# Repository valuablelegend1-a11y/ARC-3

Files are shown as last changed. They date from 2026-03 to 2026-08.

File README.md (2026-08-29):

# ARC-3



## What it is:
My ARC-3 is a 3 DoF and 3 fingered robotic arm, designed to be sleek and dynamic, while also providing complete adaptability. For example, it will feature interchangeable bases, and not require wired connection to your computer. Which will allow it to be switched between multiple locations seamlessly. This simple location management, paired with a 2:1 gear ratio for finger precision, enables it to complete a multitude of tasks. Ranging from moving a heavy mug or cup across a desk, to being mounted on the wall to flip a lightswitch at the press of a button. These are only some of the potential uses, with enough setup it could do something as precise as unloading filament from a 3D printer, or even assisting with soldering. The possibilites are endless, so here's how it's set up. It will be powered by an external power socket, using a PCA9685 module to handle current, and an Arduino R4 WiFi for the controller. For the movement it will have 4 MG995 servos, one to rotate the base (yaw) two as shoulder and elbow joints (pitch) and one more, to open and close the fingers using an advanced gear system. All the wiring from these servos will run stratiegically through the center of the arm, for an impressive outside look and no movement constrictions.

## How to use it:
1. Print & assemble: all 3D parts (see `CAD/` folder) and mount the 4 MG995 servos into the printed joints.
2. Wire it up:  connect the servos to a PCA9685 servo driver, wire the PCA9685 to the Arduino R4 WiFi via I2C (SDA/SCL), and supply servo power from an external 6V power supply through the PCA9685 V+ terminal. A detailed wiring guide is in [SETUP.md](SETUP.md).
3. Flash the firmware: open `ARC3_firmware/ARC3_firmware.ino` in the Arduino IDE or upload via `arduino-cli`. The firmware includes a static IP (192.168.4.73) so the board is always reachable over WiFi. See [SETUP.md](SETUP.md) for exact steps.
4. Run the GUI: make sure Python 3 is installed (no extra packages needed), then run `python arc-3.py`. Click **CONNECT** — the app auto-discovers the board over USB or WiFi. The IP is saved automatically so you never retype it.
5. Control the arm: use the sliders, touchpad, or keyboard (Space = claw close, Ctrl = claw open). Press **EMERGENCY STOP** to freeze instantly.

For full electronics wiring, firmware configuration, power supply recommendations, and WiFi troubleshooting, see **[SETUP.md](SETUP.md)**.

## Why I am building this:
I am creating this project for a couple reasons, I don't have much CAD experience, so I am using this to learn more about the process, and how I can be more efficient with it. Ultimately to acheive my goals faster and more effectively. I also have little practice with wiring systems, I have done some light Arduino projects in the past, but nothing of this level. So I am doing my best to learn how it all works, and how I can put different things together to make something new. Another reason is to learn to code better, I have done some programming in Python, and barely scratched the surface in Arduino code, aka C/C++, so I am trying to put what I know together, and learn more along the way to expand my understanding of the languages. 

## Notes:
1. Total cost is just over $154.75 USD, however this is including 3D printer filament, which is not included in the BOM. The price discluding filament is about $88.75 USD
2. The code is using advanced IK and trigonometry functions, which are things I have not have had much time to study, therefore they may be incorrect. If so please let me know, so I can correct any issues.
3. Any further suggestions as to design or improvements are highly encouraged and greatly appreciated.
4. My full assembly design titled 'assembly_with_electronics' *does* have electronics, but since I designed them to be safely tucked away from view, none of them are visible from the outside. 

Here is the full assembly screenshot, wiring diagram, and BOM in table format with links.

Assembly:


Wiring Diagram:


Movement Video:
https://www.youtube.com/shorts/BOCckY0NalY

BOM:
| Item | Quantity | Unit Price | Link | Notes |
| :--- | :--- | :--- | :--- | :--- |
| **MG995 Servos (4 pack)** | 1 | 6.45 | [Link](https://www.aliexpress.us/item/3256804874936334.html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) | High-torque metal gear servos for heavy-duty movement. |
| **Arduino Uno R4 WiFi** | 1 | 13.28 | [Link](https://www.aliexpress.us/item/3256810085696178.html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) | 32-bit microcontroller with Wi-Fi and Bluetooth connectivity. |
| **PCA9685 Servo Motor Driver** | 1 | 0.99 | [Link](https://www.aliexpress.us/item/3256805483968774.html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) | 16-channel PWM controller to manage multiple servos efficiently. |
| **5V 8A AC to DC Power Adapter** | 1 | 11.93 | [Link](https://www.amazon.com/inShareplus-Voltage-Transformer-100-240V-Connector/dp/B01GHN2S7Q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) | High-current power supply suitable for multiple servo motors. |
| **Jumper Wires (120 pack)** | 1 | 3.37 | [Link](https://www.aliexpress.us/item/3256803032782196.html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) | Assorted male-to-male, male-to-female, and female-to-female wires. |
| **DC Power Jack Connector** | 1 | 0.99 | [Link](https://www.aliexpress.us/item/3256806569458868.html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) | Solderless screw-terminal jack for power distribution. |
| **DC Power Jack Adapter Set** | 1 | 0.99 | [Link](https://www.aliexpress.us/item/3256803491474540.html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) | Male/Female barrel jack adapters for easy wiring without soldering. |
| **20 Gauge Wire** | 1 | 12.04 | [Link](https://www.aliexpress.us/item/3256807019321849.html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) | Stranded copper wire for main power lines and motor connections. |

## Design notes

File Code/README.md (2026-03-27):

**Python Libraries:**
All libraries used are part of the Python Standard Library; no external pip installations are required.
* tkinter/simpledialog: GUI framework and processing
* socket/threading: Networking and concurrent data handling.
* json, math, time, os, csv, datetime: Data processing and system management.

**Arduino Libraries:**
These are the libraires used in the Arduino firmware, they can be installed via the Arduino Library Manager (Ctrl+Shift+I).
* Wire.h: Handles I2C communication.
* WiFiS3.h: Standard library for Arduino UNO R4 WiFi.
* Adafruit PWM Servo Driver Library: Created by Adafruit. Used to control the PCA9685 PWM driver.

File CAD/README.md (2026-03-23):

CAD files for the ARC-3 arm, including both .step/.stp and .f3d/.f3z(native Fusion) file types

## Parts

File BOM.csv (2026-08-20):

Item | Quantity | Unit Price | Link | Notes
MG995 Servos (4 pack) | 1 | 6.45 | https://www.aliexpress.us/item/3256804874936334.html?mp=1 | High-torque metal gear servos for heavy-duty movement.
Arduino Uno R4 WiFi | 1 | 13.28 | https://www.aliexpress.us/item/3256810085696178.html?mp=1 | 32-bit microcontroller with Wi-Fi and Bluetooth connectivity.
PCA9685 Servo Motor Driver | 1 | 0.99 | https://www.aliexpress.us/item/3256805483968774.html?mp=1 | 16-channel PWM controller to manage multiple servos efficiently.
6V 10A AC to DC Power Adapter | 1 | 16.99 | https://www.amazon.com/inShareplus-Voltage-Transformer-100-240V-Connector/dp/B01GHN2S7Q | High-current power supply suitable for multiple servo motors.
Jumper Wires (120 pack) | 1 | 3.37 | https://www.aliexpress.us/item/3256803032782196.html?mp=1 | Assorted male-to-male, male-to-female, and female-to-female wires.
DC Power Jack Connector | 1 | 0.99 | https://www.aliexpress.us/item/3256806569458868.html?curPageLogUid=7rojykly85oy | Solderless screw-terminal jack for power distribution.
DC Power Jack Adapter Set | 1 | 0.99 | https://www.aliexpress.us/item/3256803491474540.html?curPageLogUid=hmDfkr7eMzGi | Male/Female barrel jack adapters for easy wiring without soldering.
20 Gauge Wire | 1 | 12.04 | https://www.aliexpress.us/item/3256807019321849.html?curPageLogUid=2DqrwgtKeStJ | Stranded copper wire for main power lines and motor connections.

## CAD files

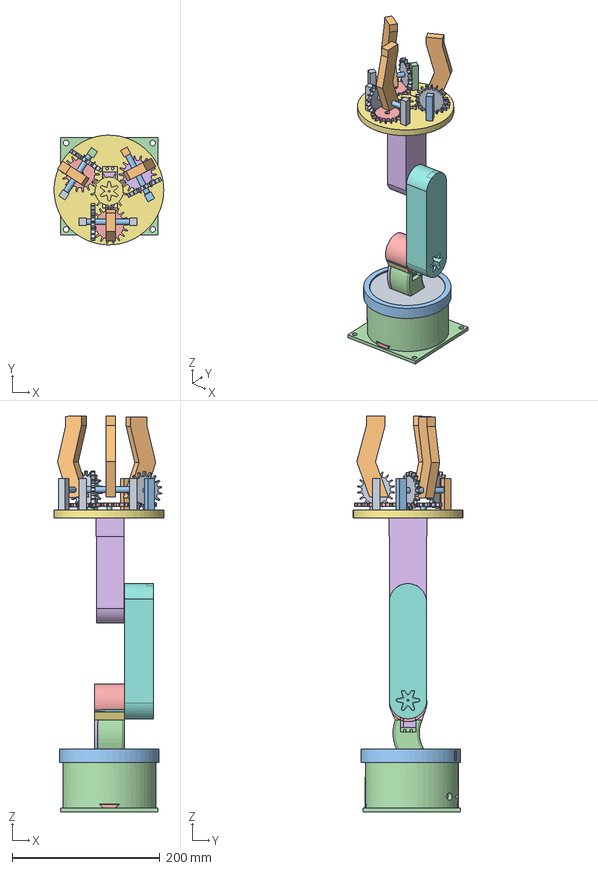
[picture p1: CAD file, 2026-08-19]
CAD/.Step File Types/assembly_without_electronics.step
148.2 x 148.3 x 535.3 mm

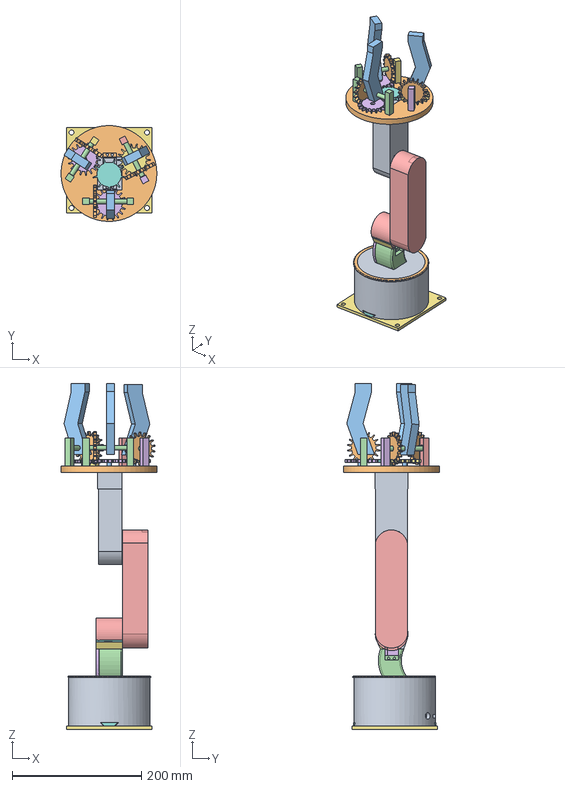
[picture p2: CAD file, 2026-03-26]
CAD/.Step File Types/assembly_with_electronics.step
148.2 x 148.3 x 535.3 mm

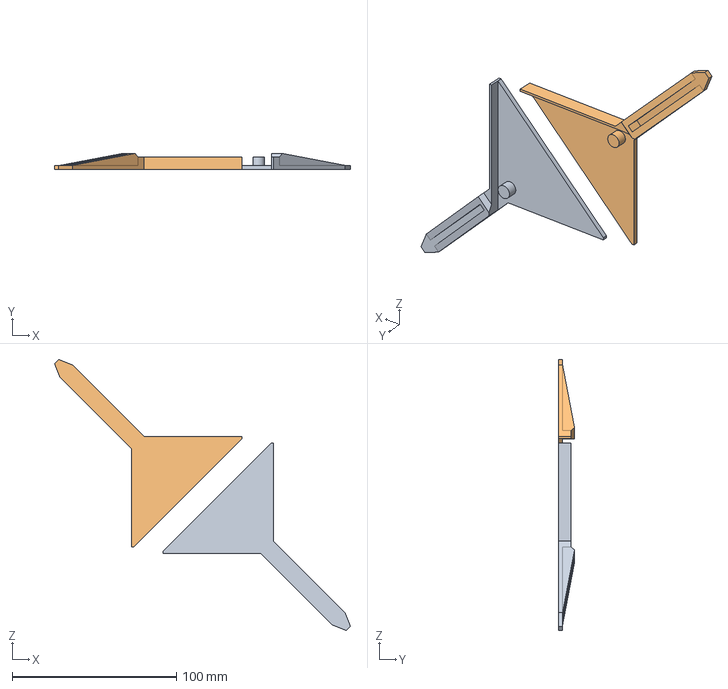
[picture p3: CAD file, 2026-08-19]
CAD/.Step File Types/base_legs.step
180.5 x 9.82 x 165.3 mm

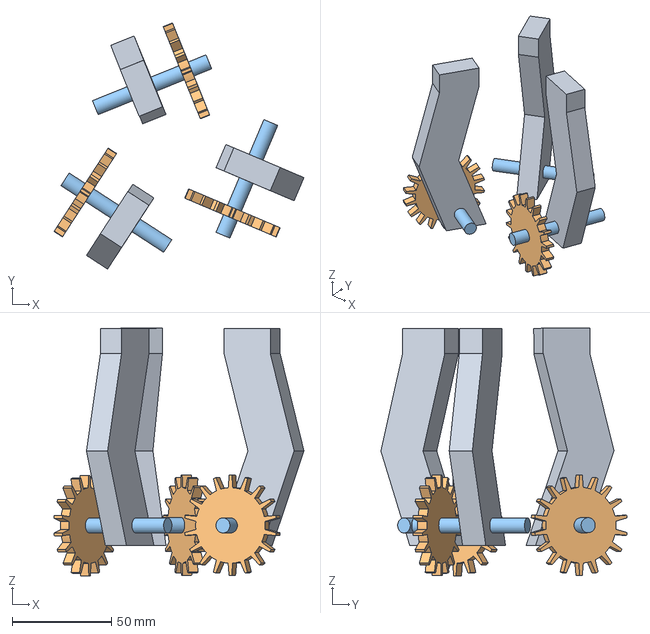
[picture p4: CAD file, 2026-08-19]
CAD/.Step File Types/Fingers.step
126.0 x 124.1 x 124.8 mm

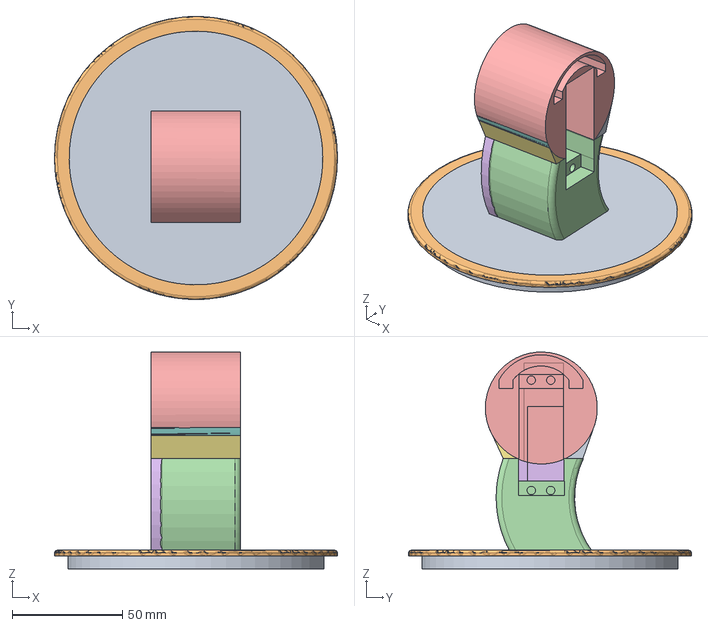
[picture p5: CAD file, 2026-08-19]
CAD/.Step File Types/base_top.step
128.4 x 128.4 x 98.4 mm

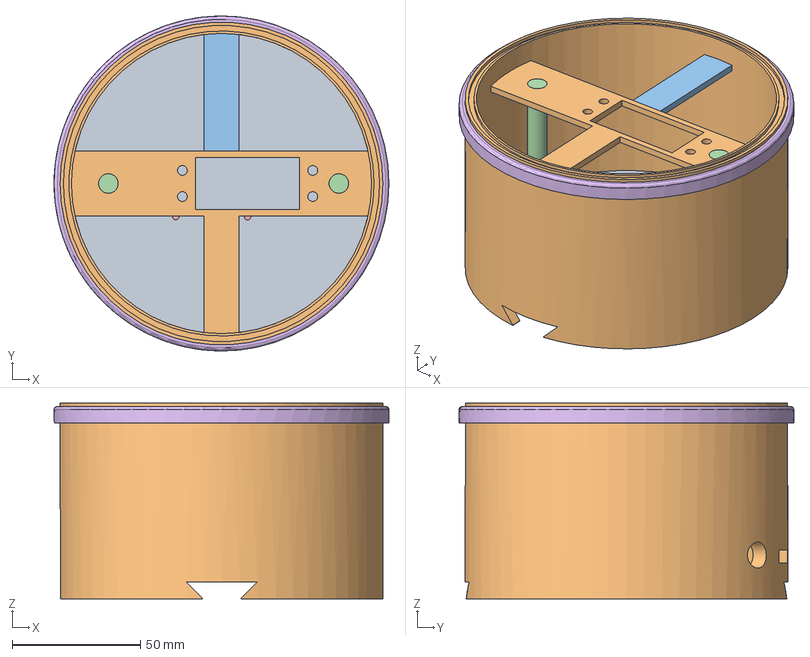
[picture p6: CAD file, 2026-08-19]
CAD/.Step File Types/base_body.step
130.5 x 130.5 x 76.2 mm

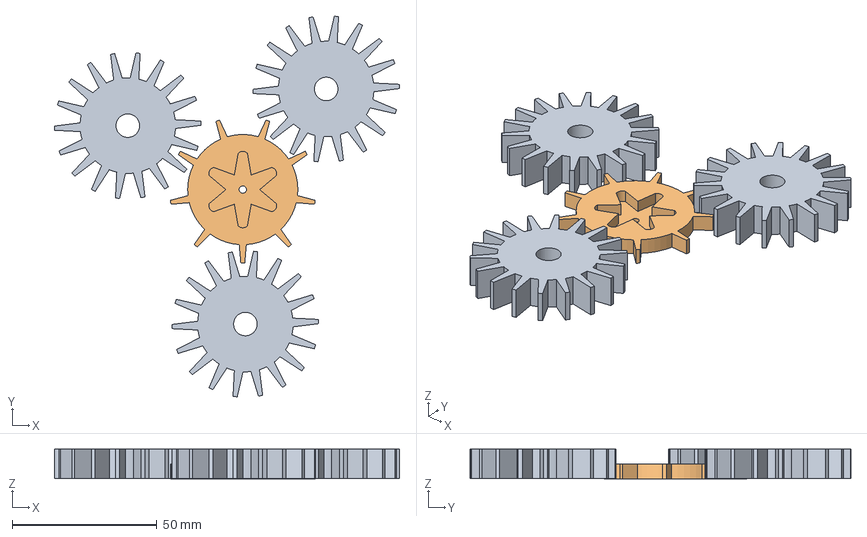
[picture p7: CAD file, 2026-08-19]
CAD/.Step File Types/finger_gears.step
119.3 x 131.7 x 10.2 mm

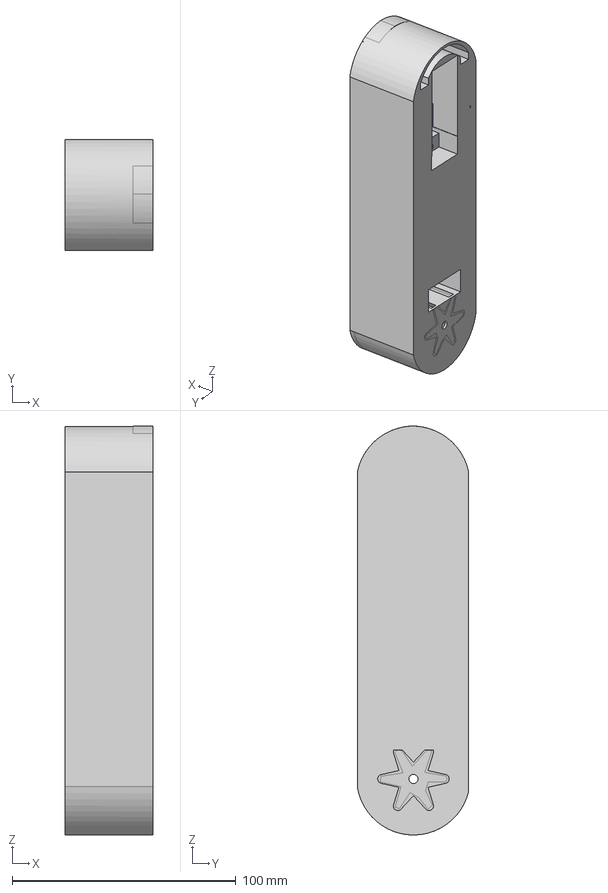
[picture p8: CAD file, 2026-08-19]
CAD/.Step File Types/arm_bottom.step
39.4 x 49.8 x 182.9 mm

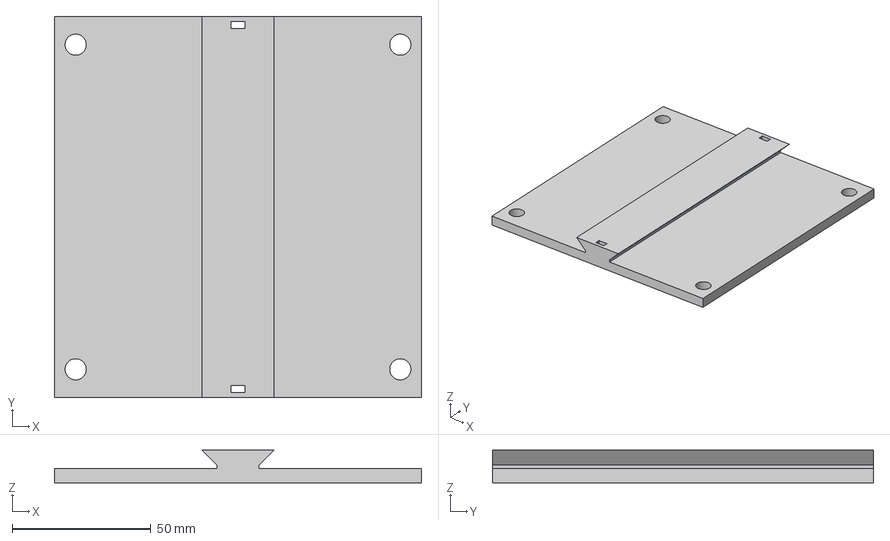
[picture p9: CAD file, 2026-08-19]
CAD/.Step File Types/base_bottom.step
132.1 x 137.2 x 11.7 mm

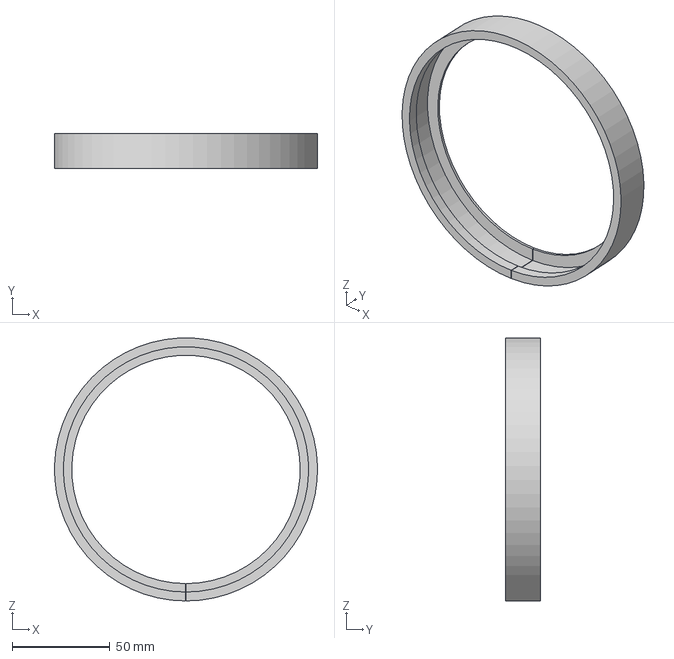
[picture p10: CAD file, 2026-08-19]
CAD/.Step File Types/base_clip_ring.step
134.6 x 18.0 x 134.5 mm

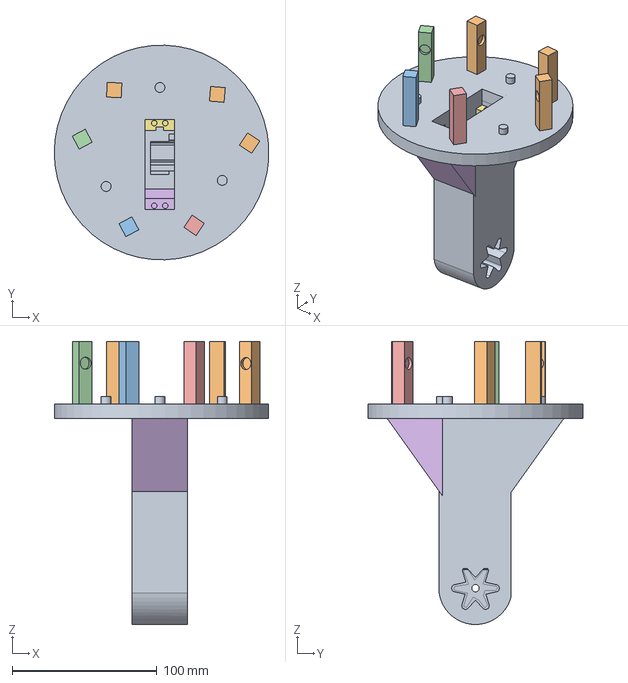
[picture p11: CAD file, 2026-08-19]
CAD/.Step File Types/arm_top.step
148.2 x 148.3 x 195.6 mm

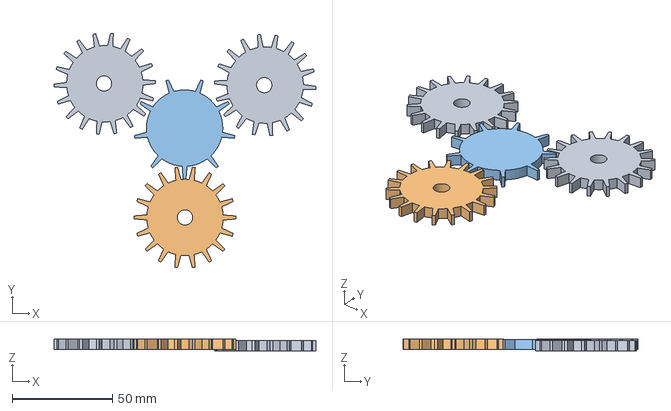
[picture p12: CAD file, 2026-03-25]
CAD/.Step File Types/gears.step
130.6 x 116.9 x 5.79 mm

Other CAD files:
CAD/Fusion File Types/Fingers.f3d
CAD/Fusion File Types/arm_bottom.f3z
CAD/Fusion File Types/arm_top.f3z
CAD/Fusion File Types/assembly_without_electronics.f3z
CAD/Fusion File Types/base_body.f3d
CAD/Fusion File Types/base_bottom.f3d
CAD/Fusion File Types/base_clip_ring.f3d
CAD/Fusion File Types/base_legs.f3d
CAD/Fusion File Types/base_top.f3z
CAD/Fusion File Types/finger_gears.f3z

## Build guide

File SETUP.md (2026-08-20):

# ARC-3 Detailed Setup Guide

## Contents
1. [Parts List Recap](#parts-list-recap)
2. [3D Printing](#3d-printing)
3. [Assembly](#assembly)
4. [Wiring](#wiring)
5. [Power Supply](#power-supply)
6. [Firmware Upload](#firmware-upload)
7. [Firmware Configuration](#firmware-configuration)
8. [GUI Setup](#gui-setup)
9. [Connecting](#connecting)
10. [Troubleshooting](#troubleshooting)

---

## Parts List Recap

See the BOM table in [README.md](README.md) for purchase links. Key components:

| Component | Role |
|---|---|
| Arduino Uno R4 WiFi | Main controller, runs firmware, hosts WiFi |
| PCA9685 Servo Driver | PWM controller for all 4 servos via I2C |
| 4x MG995 Servos | Yaw (base), shoulder (pitch), elbow (pitch), claw |
| 9V battery + switch | Powers the Arduino (switch wired to VIN and GND) |
| 6V 10A+ regulated power supply | Powers servos through PCA9685 V+ |
| 20 AWG stranded wire | Servo power bus (carries up to ~10A) |
| Jumper wires | I2C and signal connections |

---

## 3D Printing

All STL files are in the `CAD/` folder of the repo. Use PETG or something stronger like ASA or Nylon — these parts see real stress and PLA will crack at the joints over time. 0.2mm layer height works fine.

Bottom pieces and gears take the most load, so print them at 45-80% infill (more stress = more infill), gyroid pattern, with 3-4 walls. Arm pieces and fingers see less force, so those can go lower at 15-25% infill, still gyroid. The parts are designed so all electronics sit inside the base and arm body — nothing is visible from the outside when assembled.

---

## Assembly

After printing all the parts, assemble the arm before wiring anything up:

### Gear fitting
Some of the gears may not fit perfectly between the pegs out of the printer — the tolerances are what you might call "generous." If a gear is too tight to slide between the pegs on the arm pieces, trim the gear teeth slightly with a hobby knife or flush cutters until it fits. Take your time here; a little off each tooth goes a long way. The gears need to mesh smoothly but not bind, so aim for a snug fit that still spins freely.

### Securing the gears
Once the gears are in place on the arm pieces, insert a screw and washer into each peg on the arm_top to lock the gears down. This keeps them from sliding off during movement. Tighten until the gear is held firmly but still spins without excessive friction.

### Servo positioning
The slot for the servo on the arm_top is intentionally oversized — this is so you can adjust the servo's position both in height and side-to-side before tightening it down. Slide the servo around until its gear meshes cleanly with the arm gears, then secure it. Getting this alignment right is worth the extra minute; a well-aligned servo runs quieter, cooler, and with better grip.

### Spacers between arm pieces
There is a gap between the arm pieces when assembled. To fill this, create spacers by cutting a thin slice in TinkerCAD or a similar simple CAD editor, then print that piece at the exact height needed to fill the gap. Then glue the spacer onto the bottom piece of the connection so it sits flush. This keeps the arm pieces from flexing or shifting against each other during movement, and gives the whole joint a solid, unified feel.

### Servo horns
The servo horns do not fit in the slots out of the box — even with scaling and tolerances they're too tight. The best method is to use a soldering iron to melt/cut off a significant amount of material from the fins of the servo horn until it fits into the slot. Once it fits, glue it in place and add the screw to lock it down. This is much faster than trying to widen the slots themselves.

---

## Wiring

### PCA9685 connections

| PCA9685 Pin | Connect To |
|---|---|
| VCC | Arduino 5V pin (powers the PCA9685 logic) |
| GND | Arduino GND (common ground with power supply) |
| SDA | Arduino SDA (A4 on R4) |
| SCL | Arduino SCL (A5 on R4) |
| V+ | External power supply positive (6V) |
| V- (GND) | External power supply negative (GND) |

### Servo connections to PCA9685

| PCA9685 Channel | Servo | Function |
|---|---|---|
| 0 | MG995 #1 | Yaw (base rotation) |
| 1 | MG995 #2 | Shoulder (pitch) |
| 2 | MG995 #3 | Elbow (pitch) |
| 3 | MG995 #4 | Claw (gripper) |

Each servo has a 3-pin connector (signal / VCC / GND). Plug into the PCA9685 headers matching the channel — signal wire to the PCA9685 signal pin, power and ground to the outer pins.

### Power wiring

The Arduino is powered by a 9V battery wired through a simple switch to the VIN and GND pins on the Arduino. The PCA9685 VCC is plugged into the Arduino 5V pin for its own logic power. Run 20 AWG stranded wire from the external servo power supply's positive and negative terminals to the PCA9685's V+ and V- screw terminals. Do not power the servos from the Arduino's 5V pin — the servos will draw too much current and reset the board.

### Critical: common ground

The power supply GND, PCA9685 GND, and Arduino GND must all be connected together. Without a common ground, I2C signals will be unreliable and servos will glitch.

---

## Power Supply

This is the most important hardware decision. MG995 servos draw ~0.5A holding and up to ~2.5A at stall each.

### Recommended
A 6V, 10-12A regulated supply (e.g., a 6V/10A or 6V/12A AC-to-DC adapter). Set output to 5.8-6.0V if adjustable (MG995 spec is 4.8-6V; PCA9685 V+ max is 6V).

### Why 6V instead of 5V
Running at 6V gives noticeably more torque and headroom before servos stall. At 5V, the shoulder holding the full arm weight can drop when another servo starts moving — at 6V it holds firm.

### Wire gauge
20 AWG stranded wire works fine for the servo power bus. Thin jumper wires will sag under load and defeat the purpose of a beefy supply.

---

## Firmware Upload

### Option A: Arduino IDE
1. Install the Arduino IDE (2.x).
2. Go to Tools > Board > Boards Manager, search for `Arduino UNO R4 Boards`, and install it.
3. Open `ARC3_firmware/ARC3_firmware.ino`.
4. Select Tools > Board > Arduino UNO R4 WiFi.
5. Select Tools > Port > COM10 (or whichever port your board appears on).
6. Click Upload.

### Option B: arduino-cli (command line)

# Install (one time)
arduino-cli core install arduino:renesas_uno

# Compile
arduino-cli compile --fqbn arduino:renesas_uno:unor4wifi ARC3_firmware/

# Upload (replace COM10 with your port)
arduino-cli upload -p COM10 --fqbn arduino:renesas_uno:unor4wifi ARC3_firmware/

After upload, the board's serial monitor (115200 baud) will print the WiFi IP address and confirm servo initialization.

---

## Firmware Configuration

Open `ARC3_firmware/ARC3_firmware.ino` and edit the following at the top of the file:

### WiFi credentials

const char* WIFI_SSID     = "YOUR_WIFI_NAME";
const char* WIFI_PASSWORD = "YOUR_WIFI_PASSWORD";

### Static IP (recommended)
The firmware ships with a static IP so the board's address never changes between reboots:

#define USE_STATIC_IP 1
#if USE_STATIC_IP
IPAddress LOCAL_IP(192, 168, 4, 73);
IPAddress GATEWAY_IP(192, 168, 4, 1);
IPAddress SUBNET_MASK(255, 255, 252, 0);
#endif

LOCAL_IP: Set this to a free address on your network (avoid the router's DHCP range). GATEWAY_IP: Your router's IP (usually 192.168.x.1). SUBNET_MASK: Usually `255.255.255.0` (or `255.255.252.0` for /22 networks — check your PC's Wi-Fi config to confirm).

If you prefer not to set a static IP, set `#define USE_STATIC_IP 0` and the board will use DHCP (the IP can change between reboots).

After editing, recompile and reupload.

---

## GUI Setup

The GUI (`arc-3.py`) requires only Python 3.8+ with its standard library. No pip install needed — tkinter, socket, threading, json, math, and csv are all built in.

python arc-3.py

### What the GUI provides
- Sliders for each servo angle (yaw, shoulder, elbow, claw)
- Touchpad for XY control with inverse kinematics
- Keyboard controls: Space = claw close, Ctrl = claw open
- Position save/load (.arc3 JSON format)
- Motion recording and playback
- Connection panel: USB (auto-detect) and WiFi

### Settings
The app saves your last WiFi IP and port to `arc3_config.json` automatically — you never need to edit the IP in code after the first successful connection.

---

## Connecting

### First time (USB)
1. Connect the Arduino to your PC via USB cable.
2. Launch `arc-3.py`.
3. Leave the connection field on AUTO and click CONNECT.
4. The app scans USB ports, finds the board, and connects.
5. The app auto-detects the board's WiFi IP from the STATUS response and saves it for next time.

### Subsequent use (WiFi)
1. Launch `arc-3.py`.
2. The saved IP should already be in the connection field.
3. Click CONNECT — the app connects over WiFi. No USB cable needed.

### If WiFi fails
The firmware auto-retries WiFi connection every 10 seconds, so it will come back online on its own. Plug in USB, hit CONNECT — the app re-learns the board's current IP. Make sure your PC and the board are on the same WiFi network. Disconnect any VPN (e.g., Proton VPN) before connecting — they block local network traffic.

### Servo test
The TEST SERVO button in the connection panel sweeps a single servo channel (0–3) back and forth. Use this to diagnose a dead servo or verify wiring. The claw is channel 3.

---

## Troubleshooting

### "timed out" on connect
Board may still be booting — wait 15 seconds after power-on. WiFi link may be weak — check distance to router, reduce interference. VPN active — disable it. The app retries 3 times automatically; if it still fails, plug in USB to verify the board is alive.

### Board not found on USB
Close Arduino Serial Monitor / any other serial terminal using the port. Check the USB cable is data-capable (not charge-only). Verify the port in Device Manager (should show as `Arduino UNO R4 WiFi`).

### Servos not moving
Check power supply is on and connected to PCA9685 V+/V-. Verify the PCA9685 I2C wiring (SDA/SCL). Use the TEST SERVO button to isolate a dead channel. Ensure the servo connector is oriented correctly (signal wire to the signal pin).

### Servos jittering or glitching
Power supply too weak — upgrade to 6V/10A+ and use thicker wires. Ensure all grounds are common (PSU, PCA9685, Arduino).

### One servo drops when another moves
Classic power sag — the moving servo's surge drops voltage below the holding servo's threshold. Fix: use 6V supply, thick wires, counterweight the upper arm to reduce shoulder holding load.

### WiFi connects but IP keeps changing
Enable `USE_STATIC_IP` in the firmware (see [Firmware Configuration](#firmware-configuration)). Or set a DHCP reservation on your router for the board's MAC address.

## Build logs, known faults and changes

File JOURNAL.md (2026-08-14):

**3/20/2026 - I created basic paper drawings of my concept.**

I started off by creating some very basic and crude 2D paper drawings, that are not to scale, but helped me get a good picture of how I wanted the project to come together. There is one of the whole deign concept, one of the claw, and one of a simple wiring diagram, the MG995 and MG90s servos will all channel throughout the arm down to the PCA9685, which will connect to the arduino uno, both of which will be powered by an AC-DC converter. 




*Time Spent: 2 Hours*

------------------------------------------------------------------------

**3/21/2026 11 AM - I designed the main body with support and alignment.**

I then started designing it all from the ground up in Autodesk Fusion (formerly Fusion 360).
For the main body or 'base body' I started off with a 5 inch diameter outer edge, with a roughly 0.2 inch thickness to form a cylinder, I then extruded it to a height of 3 inches, to fit all electronics and mounts. From here I added a simple divider 0.3 inches from the bottom of the cylinder, so the base mount and electronics are separated. Next I measured out specific holes in the outer shell, that will fit the female sockets of both the Arduino input cable, and a DC cord for power from an outlet converter. After that I added a reinforced frame with screw holes, for the MG995 servo in the base, to ensure it was secure and correctly positioned, with simple support pillars for added strength. 


*Time Spent: 5.5 Hours*

----------------------------------------------------------------------------

**3/21/2026 4 PM - I created my BOM in csv format with links and pricing.**

I had a bit more time than I expected today, so I decided to find all the specific parts I had planned, and put it in a BOM.csv document in my GitHub repository. While I was researching I found better pricing than I initially thought, and was able to slightly cut costs without hindering performance. I also realized my initial plan to use an MG90S servo for the fingers would likely not be enough, so I decided to just go with all MG995 servos, for both the joints and fingers, to simplify things and ensure functionality would not be limited. I also decided on specific filament types, choosing PETG for its ease of use and strength to weight ratio, along with better flexibility under tension. The specific filament brand I use is Elegoo, as that is the brand of my 3D printer, and the quality has been good so far, the only downside is a $15.00 shipping price, however that is including sales tax, so it may even out.


*Time Spent: 2.5 hours*

--------------------------------------------------------------------

**3/22/2026 - I created the Base Top to be fitted and rotatable.**

At this point I got started on the top piece, the 'base top' that will fit on the main body, be fully rotatable, and be directly connected to the base MG995 servo. It was fairly uncomplicated to make the main circular portion to fit on top of the body, I did it by making a thin cylinder that fits the inside of the body cylinder (with tolerance) and a slightly wider portion overtop of that, that covers it all up nicely. For the connection to the servo I decided to make a cutout that will perfectly fit the servo horn, so the horn can be screwed onto the servo, and then glued into the base top. After that I made a structure off the top of the 'lid' portion of this piece, to give distance between the yaw and pitch joints. I started out with a basic rectangle, and decided to go with a slightly more curvy shape and fileted edges, for a more aesthetical design. on top of this I put a 2 inch diameter circle, which I extruded to the length needed to fit the second MG995 servo. I made a cutout to fit the servo, with screw holes aligned for the edges to be aligned where needed, and included tolerance to ensure it fits correctly. I also left it slightly offset for stability of the next piece, and created a loft to smooth out the edges. 


*Time Spent: 5 Hours*

-----------------------------------------------------------

**3/22/2026 9 PM - I built the first arm segment.**

Next up was the first arm segment, the 'arm bottom' which I went back and forth for a while trying to get the design to look sleek, while also fitting all the components correctly and not hindering and capability. To do this, I started by creating a vertical rectangle, with fileted edges and a space for the servo horn or the previous MG995 servo, just like on the base top. After that I added a circular portion on top, that again, fit the MG995 servo for the next pitch or elbow joint, with dedicated screw holes and adjusted tolerances. On this piece I also left the servo hole portion slightly offset from the main portion, to allow for more stability and direction. There were slight complications with my design however, and I had to redo multiple sections to allow the servo to fit correctly. To be specific, I created the servo hole first, then I later on repositioned the top part, which offset the ledge and the screw holes, and caused me to spend more time fixing alignment. Only after I had fixed that issue, I created the loft, which, unbeknownst to me, also filled in part of the servo hole and ledges.

Fortunately it was a simple fix to just re-cut out the servo hole, and not create a loft that restricted that space again. Then I slightly modified the design, so it was much more sleek and fit the servo and overall the way I wanted it to look, and I fixed some slight issues with the edges and repositioned the top portion.


*Time Spent: 6 Hours*

-----------------------------------------------------------------

**3/23/2026 - I made channels through the designs for wiring.**

Today I decided to solve wiring, I need to have servo wires run from the fingers and other joints, all the way to the Arduino and power in the base. To do this, I cut out slots right above each joint connection, and ran them down behind the servos and into the next piece. I used an arc shape so there would be plenty of movement freedom for when the arm was rotating. I then cut a small hole in the bottom of the base lid to ensure all the wiring can flow smoothly down into the base. After I did all this I realized it had slightly messed up my arm pieces, by clearing out areas needed for internal support and stability, so I went back through every piece and slightly altered it to ensure the wires could run correctly without compromising structural integrity.




*Time Spent: 3 Hours*

--------------------------------------------------------------------

**3/23/2026 5 PM - I designed the arm top to connect the fingers.**

Now I am starting the top portion that connects the fingers to the rest of the design, the 'arm top'. I started off with the previous arm piece, and cut it in half to use just the bottom portion. Initially my plan was to have each finger with it's own servo, but immediately when I started designing, I realized that was highly inefficient and resorted to a gear system to control all the fingers simultaneously with one servo. I needed a place to align all these gears, so I put a 5 inch circle on top if the half-arm piece I made earlier, and extruded it to 0.4 inches thick. I needed a I put three small rods in a triangle shape, to later align the gears correctly around the servo gear, and messed with the diameter for a bit to make them small enough to fit on the inside of the gears. After this I decided to make some support columns for the vertical gears, so they could freely rotate but be secured to the hand as a whole. Initially I just made them as vertical rectangular beams, then I added simple slots in the sides, so the rod to hold the fingers would be secure.



*Time Spent: 5 Hours*

-------------------------------------------------------------------

**3/24/2026 - I created the gears with the correct teeth ratio.**

Next up was the actual gears, I started out by drawing a simple diagram of how I wanted the gears aligned and shaped, then got going on creating the real versions in CAD.

At first, since I am new to designing, I was hand creating every tooth, which was very time consuming and not perfectly symmetrical either. At first I was using my makeshift technique to create gears in a 2:1 ratio, with 5 and 10 teeth, but when I realized I would want more teeth on both gears, I decided to learn a better technique to not spend hours deigning them a second time. I found the method of copying the gear tooth sketch, and rotating it around the center circle of the gear by way of the move/copy tool. This sped up my project a large portion, and before too long I had correct gears with 10 and 20 teeth, along with a much more symmetrical design. I spent some time aligning them how I wanted, to test how they would function. As I did this I realized that realistically I would want a number of teeth divisible by 3, for the three fingers to be aligned the same without hours tweaking. So I created yet another simple sketch, just to ensure I could still visualize what I wanted.

And even though my second method of designing gears was faster, it still had it's downsides, so I went in search of a more efficient way. I found the obvious answer after not too long, the circular pattern function, which can duplicate a sketch around a circular axis evenly. I got it all set up, and sure enough, in less than 10 minutes I had perfectly symmetrical and aligned gears with the correct tooth amounts of 9 and 18.


*Time Spent: 4.5 Hours*

--------------------------------------------------------------

**3/24/2026 5 PM - I made the fingers with aligned gears.**

Today I started working on the fingers themselves, I started off with a slanted line, it was 1.5 inches long and at a 75 degree angle, I added a simple parallel line, and connected them at the bottom. Then I made another set of parallel lines of the same length, slanted back the other way, and connected those at the top. Upon testing the length compared to my other parts, I realized they would be a bit short, so I increased all the lines length to 2 inches, and that fit my size expectation much more. I then extruded them to a half inch, and extruded the flat face that would be the top, so it had a flat surface. After that I created a new gear, that would line up with the horizontal gears on the previous arm piece, and therefore open and close the fingers. Next I added a simple rod through the center, that would rotate on the pillars of the arm top, to give freedom of movement but retain connection to the overall structure. Then I simply duplicated the design twice, to have three fingers of the same dimensions without any guessing. I took a few minutes arranging them to how they would be setup in the end design, and added them to the assembly design I have. After I got them positioned, I realized the gears would not quite line up, so I rearranged them all, tried again, failed again, rearranged again, and got them to a position I was satisfied with. Then I saw that my rods running through the fingers did not align with the slots in the arm top, so I went back and redid those again as well. After getting it all set back up, I saw the gears were slightly too low (as to too far right before) so I realigned them all, and finally got it all setup correctly.



*Time Spent: 3.5 Hours*

---------------------------------------------------------------------------------

**3/25/2026 11 AM - I designed the base bottom with an interchangeable system**

Lastly for the modeling, I needed to get the base system set up, the 'base bottom'. I want the base to be able to be interchangeable, so I can have multiple of them, and easily move the arm around without unscrewing the whole base. To start I wanted to use an interlocking pin system, so I could slid it on and rotate it into place, so I started designing it. And very quickly I realized that this would be highly inefficient, as each pin would have limited size, and it could easily slide out. So I scrapped all that, and decided to start fresh. This time I decided to use a dovetail design, as it is super easy to both design, and to use in general. So I made a basic trapezoid on the top of my first baseplate, and created a matching sized cutout on the base of the arm (with tolerance). For the actual base plate I just made a simple square, with a slightly bigger length than the base body, and a hole in each of the corners for screws. This will allow my to create at least two, one for my desk and one for the wall, that I can bolt on and leave there and just remove the arm.



*Time Spent: 2.5 Hours*

-------------------------------------------------

**3/25/2026 3 PM - I added the wiring diagram**

Now that all the modeling is done, I decided to add my wiring diagram. So I researched, and ultimately decided to use EasyEDA, because it is free, web based, and very well liked. I first added on my Uno R4, and a basic power supply representation. I could not find the exact model of PCA9685 board that I am using, so I picked the closest one and added that as well. Then I went about connecting these two together, and to the power supply. After I ensured I did not have any wires crossed (quite literally) I added the MG995s to the diagram, in the actual PCA9685 I am using, the plug ins for all three servo wires are aligned, but in this board I found they are not. So I decided to just connect the wires to the literal power and signal wires they would be drawing from, even if they are in a different spot. I then saved it as a PDF and added that to my repository, and attached a separate screenshot here.


*Time Spent: 1.5 Hours*

--------------------------------------------------

**3/26/2026 - I made two separate assemblies**

Now that the majority of all the modeling was done, I decided to combine my parts into two separate assemblies, one with electronics, and one without. I started from the bottom up, inserting everything into the first assembly -the non-electronics one- and arranging them all in the orientation they are meant to be in. Most of it was pretty simple, adding parts and moving them around, I had a few slight hiccups with accidentally moving them after initial orientation, which in turn messed up the geometry of the original design. However they had simple solutions to ensure nothing would be ruined. After I completed the first assembly, I started work on the one with electronics. I found CAD models for the servos, boards, and the like on GrabCAD, and set to work adding them to a file. This proved to be a slightly more complicated process, as some parts of my designs had gotten messed up along the way, so I had to redo multiple things so it all would fit correctly. Since it would be slightly difficult to add wires twisting the directions they would need to be in the design, I decided to add all components except wires, and just make a separate wiring diagram. Note: my particular design has all electronic components hidden on the inside, they are there, just not open visible without taking it apart.



*Time Spent: 3 Hours*

**3/26/2026 3 PM - I added a simple cutout for bearing balls**

Secondly today, I realized I would want some bearing balls in the top portion of the base pieces, so they would rotate smoother and with less scraping. So I found some basic ones that fit my needs, and added them to my BOM with pricing and the link. I also realized that this brought my cost back up evenly to $180, as I found a cheaper part option the other day that lowered cost. Then I made a simple cutout in the top and bottom of my base body and base top pieces respectively, so everything would fit and turn smoothly.



*Time Spent: 30 Minutes*

**3/27/2026 - I wrote the Arduino firmware**

Now that everything manual is established, I went to work on the code. I will be writing some firmware to put on the Arduino Uno R4, and some additional Python code for precise calculations and smooth movement, along with a simple GUI for user-friendly control. To start, I built the Arduino code, I haven't had a lot of experience building INO files, but I did some research and got to work making it all function. I used the WiFiS3 library which is the Uno R4's built in library, and added the Adafruit_PWMServoDriver
library to use with the PCA9685 to control the servos. I decided to set it up so the commands could come in using ASCII with \n at the end acting as an 'enter' button, so it puts the bytes into cmdBuffer until it sees \n, then calls handleCommand to run it. Here is how I handled the PWM math. Since MG995 servos use standard RC PWM: 50Hz frequency and 20ms period, with pulse width between 500Us (0°) and 2500Us (180°), and a 12 bit counter, starting from 0 that's a total of 4096 ticks per period, which means the conversion is ticks = pulseUs * 4096 / 20,000, meaning the setPWM call sets the on ticks to 0 and the off tick to ticks, which produces ticks/4096 * 20ms pulse at the output pin.


*Time Spent: 2.5 Hours*

**3/27/2026 3 PM - I coded the Python script**

After completing the Arduino firmware, I got started on the Python program, which will be mostly for the angle input and GUI, with some added benefits. i decided to put calculation, communication, and visualization into three separate lanes, the Main Thread handles drawing the Tkiinter window, which was a process to figure out, because Tkinter doesn't like multi-threading, so I used afteridle to 'drop' and 'pick up' the thread. Then the Motion Thread ensures it runs at 50Hz, so the servos dont just jump to the target, but rather glide smoothly to the set position. Lastly an AI Socket Thread that sits and waits for commands, it doesn't move the servos itself, it just updates the targetangle variable, so the Motion Thread can notice it and act upon it. Next I used an IK solver to work trigonometry to turn a 3D point into servo degrees. it does this by treating the arm as a triangle, and using the Law of Cosines to calculate the interior angle of the elbow. It also has a simple 'elbow up' flag, to ensure it does not try to reach the selected position whilst flipping the orientation back and forth. Also some simple coordinate mapping ensures that the servos understand that their horizontal (90 degrees) is actually up, and 0 degrees is actually flat, it does this by using 90 - degrees(rad_angle) to translate the servo position correctly to what we see vs what the servo thinks. Then I added all the filler and def commands, and did brief revising to have it be somewhat clean, and added simple comments for most commands to help explain functions.


*Time Spent: 4 Hours*

**3/29/2026 - I finished my repository and added licenses**

Lastly for the planning portion of this project, I wrapped up my GitHub Repository. This included editing the README with text sizes and correct images, adding simple explanations to my other folders for extra direction, and editing my journal and BOM files. I then created a license file, and added all the specifics of how I wanted it to be used, including adding an MIT license for the code, and a CC BY-SA 4.0 for everything else. To finish it off I did a quick once over of every file, image, folder, and the like, just to ensure that everything was in place how I wanted it to be.


*Time Spent: 1 Hour*

**4/9/2026 - I edited designs and removed a soldering iron from my BOM**

I decided to edit the servo horn securing situation, so the parts would hold together without glue or other methods, and can be
easily removed and edited as needed. I also updated my BOM to remove a soldering iron from my costs, as that is not a part of my materials list.


*Time Spent: Half an Hour*

**4/26/2026 - I edited my BOM with better price management**

So after my initial project review, I was encouraged to use better cost optimization and find better prices. So I searched for a while, found some better deals and prices, and added everything to both my BOM.csv file and in my readme. I also removed filament from my BOM, as I found out it would not be funded. This lowered my total to $51.00 USD, or $107.00 USD including filament, which I will buy myself.


*Time Spent: 1 Hour*

**6/13/2026 - I started printing!**

So I finally got the filament, and decided to start on printing the parts from the ground up (mostly).
I started off with the 'base_body' piece, which is the main cylindrical body that will hold the power converter, arduino board, and the base servo for pitch (left-right) movement.
I pulled the design into the slicer, and oriented it to lay on it's side, so that and tension on the piece will not just rip between the layers and snap it. I used 75% gyroid infill, for high density but without wasting material. Then I added two pauses to the print, to switch the filament from black to green, then back to black to get a nice center green stripe. It used about 200g of filament and took a bit over 6 hours, and turned out very well with some light support scarring but no other issues.

WIN_20260613_19_17_12_Pro

*Time Spent: 2 Hours*

**6/14/2026 - I iterated and printed the next part**

So for the next part, the 'base_top' I wanted to print it on its side for better integrity. I got it all sliced, and it only used a little more support than it would if it was in the suggested orientation. I got it all set up and started printing it. About 3 hours in, I went to check on it, only to find that it spaghettied horribly (filament strands everywhere and trying to print on thin air). So I modified the orientation, added beefier supports, and edited settings for a hopefully smoother print. After another 3 hours of printing, at the exact same second it failed again. I still have no idea why this happened and even the footage doesn't reveal it. For this one however, the completed portion was more salvagable than its successor, so I was able to test attaching half of it to the previous piece. This revealed that although they would fit together, they would not lock tight enough, and the clips were so weak that even removing support structure snapped two of them. So I took a step back, fixed the compromised faces in CAD, and switched the part orientation instead to the suggested side. The reasons I didn't do this originally were 1. It could make the part slightly less strong under load (I raised the wall count and infill to compensate) and 2. I couldn't put that nice green stripe up the center like the last piece (I will have to later glue on a piece of green or just go without it). Ultimately the part turned out and worked very well with just some minor sanding.

WIN_20260614_17_00_31_Pro

WIN_20260614_16_46_46_Pro

*Time Spent: 4 Hours*

**6/16/2026 - I made my best 3D print ever!**

The next piece in my lineup was the 'arm_bottom' piece, which is the center of the arm, and the only piece featuring the servo moving it and its own servo rotating the same way! This piece was fairly simple to setup, I just used the auto orientation and added two simple pauses for the color change. I also lowered the infill to 65%, because this part is so solid that any more than that is just wasting material. It printed in a few hours, and everything went perfectly. When it finished, I was in shock by how perfectly it came out. With no supports and no odd angles, it had the perfect setup to print amazing, and it did not disappoint. There were no botched sides, no random strings, and no print scars whatsoever. It truly is a masterpiece.

WIN_20260616_12_49_25_Pro

*Time Spent: 1.5 Hours*

**6/23/2026 - I made the next piece**

Next up to create was the 'arm_top' which is a very important piece, because it will hold the fingers, gears, and the servo to move those. It is also set up in such a way that it is rather difficult to print, as there are multiple different angles and parts to it. I set this piece up using a much lower infill of 45%, because it is not taking as much stress from multiple angles. The first version used auto orientation, and pretty similar support settings to it's predecessor. It got done with the first half perfectly, but about 2 hours in, it completely flopped. Stringing everywhere, sides peeling off the bed, and messed up sides. So I messed with the support settings for a bit, changed the angle to fully sideways, and wiped off the build plate for better adhesion. This one worked perfectly, it came out smooth and the supports peeled right off. I realized after the fact that I had not done a thorough wipe down of the plate, and that was likely why so many prints had failed.

WIN_20260616_12_49_51_Pro

*Time Spent: 2.5 Hours*

**6/23/2026 3:59 PM - I printed the gears green**

After all the previous prints, it was very satisfying to have a simple print that basically couldn't fail: The gears. They are flat on the top and bottom, rather small, and overall a simple structure. I set them up in the slicer at 80% infill since they will be under a lot of strain, and set up the printer with just green filament for them. Since they will be laying down, and that is the orientation I am printing them, doing multiple colors would be useless. So i did just green to get a nice color pop for the top, and because that is what i have the most of. They printed great, super quick and no issues, and they fit perfectly on the previous piece. Another print down.

WIN_20260623_15_53_42_Pro

*Time Spent: 45 minutes*

**6/24/2026 - I created the fingers**

The next piece to do was the fingers. I knew it would be crucial for these to print well, as they are doing all the -quite literally- heavy lifting. So I set them up in the slicer, using the same 80% infill as the last piece for strength, and 4 walls for thickness. I got them set up to print, and just as they started, I realized that I had forgotten to add a color switch. I went to just add it, but I realized it would not look right with the rest of the pieces, and at the same time I noticed how bad the orientation was. They were vertical, meaning tension on them could pull them apart between the layers, and printing time would just be very long. So I reoriented them (I dont have a picture of that) and added the color change. They printed great, and fit in the slots on the 'arm-top' perfectly.

WIN_20260623_16_17_50_Pro

Time Spent: 2 Hours

**6/26/2026 - I made the final piece!**

Then came the time to create: The last piece, the 'base_bottom'. Which is a very crucial piece, as this is the actual base that the whole arm will be mounted on. The first version is actually pretty simple, it uses a dovetail joint to nicely slide onto the body, and 4 simple holes to be screwed into the desired surface. Later on there will be multiple different bases set up at different locations, so I can just slide the arm off one base and onto the next. But for now, this simple one will work great for testing! I got it sliced up at 80% infill and 4 walls for high strength, and oriented it on it's side. Which was rather sad to do, because it would have been great to print it fast and flat, but having good layer direction is better in this case. I first decided to print a quick test piece of the dovetail joint, because it worked great in the assembly, but tolerances change things. The first one did not fit at all, it was just a bit misaligned and it made the whole thing wayyy off. The second one was better, but it was very very tight, not really what you want for quick switchability. Then the final test piece worked great, so I printed the final version with those updated measurements. It came out very well, and fit as expected.

WIN_20260626_16_36_20_Pro

*Time Spent: 1.5 Hours*

**7/4/2026 - I received the parts! Well, most of them.**

My electronics finally came in! They arrived intact, and at first it seemed that they had all successfully arrived. But when I got to the end of the package, I saw there was no AC-DC converter(power cable whatsoever. Thankfully all the other components came in and looked great, and it was great to see them all lain out on my workbench. Unfortunately the package weight suggested that potentially the cable was at one point in the package, and must have been later lost in transit or stolen. So I reached out to AliExpress and the manufacturer(which I didn't expect to hear back from). And began the waiting process of getting the refund to order a new one. The next day I checked on the refund status, only to realize that they wanted 'more proof' that I had not received the item. Which is kinda difficult to prove, as I literally did not receive it. So I just did my best to emphasize the fact that I received the other 7 items, and the package weight showed that at one point the cable was likely inside. For now I will continue to contact the manufacturer and the shipping company, and hope one of these three will respond so I can go about purchasing a new part. 
WIN_20260704_18_59_43_Pro


*Time Spent: 1 Hour*

**7/6/2026 - I tested the parts**

Now that most of my parts were in, it was time to test them and hope my tolerances were enough. And immediately upon pulling the servos out of the bag, I could see that they were not quite as described. On each one on the side where the wires come out, there was a little plastic knob protruding from the side to cover the wire entrance. This wouldn't have been an issue, except that this was not on any of the seller images(I went back and checked) so I had not factored it into my designs. And unfortunately this meant that the servos would not fit into any of the parts right away. Thankfully on the three of the pieces it was fairly simple to carve out a slot, with just a bit of time and elbow grease. And all in all the other parts appeared to look good, and there was nothing else that really needed fitting tests, so everything should go as planned. --see next journal entry because one piece did need to be redone but it is a long process so I'll put it in a separate entry--
WIN_20260706_12_52_27_Pro
WIN_20260706_13_02_02_Pro

*Time Spent: 2 Hours*

**7/6/2026 2 PM - I redesigned a part**

So unfortunately since the servos had an unexpected piece attached, I had to redesign one of my parts. Which wasn't all too bad, considering that there were some other slight issues with it that could've been ignored, but were worth fixing while I was at it. So I pulled the design back up in fusion, and edited a bunch of the positioning so everything fit better. I got it printing right away and it seemed to turn out as expected(9 hour print) but then the realization hit, in my midnight redesign spree I had accidentally shifted the space for the servo a half-inch in the wrong direction. So now instead of being 0.5in off alignment, it was a full inch off, which wouldn't even partially work. So I went back to the drawing board, undid all my work, and shifted it back in the other direction. This turned out to make the space for the servo stick slightly out of the side of the part, which was something I was really trying to avoid, since this was meant to be a 'sleek and adaptable' robotic arm. This lead to more redesigning to cover up the slot, and in turn actually gave the piece a slightly new look that I actually enjoyed. And since the new design gave the circular top portion more support, and that was the only part that was really under any stress, I was able to lower the infill to just 35% (down from 45%) which basically compensated for the added material of the redesigned portion.
WIN_20260706_14_23_59_Pro


*Time Spent: 2.5 Hours*

**7/16/26 - I designed and printed the feet**

Next thing to create was the 'base_feet', which I decided to design to literally slide onto my current base piece, for easier connection and less redesigning. I started off with just the basic corner shape and a cylinder in the corner to slot in nicely, then the foot coming off the side for the stability. It printed quick and came out well. The tolerance was absolutely perfect, like I genuinely have only ever achieved this perfect of a fit once or twice, and this is one of them. And since it fit, I decided to head back to fusion and give it a little bit of a stylistic look, and it also will increase the strength when under a lot of tension from the leaning arm. 



*Time Spent: 1 Hour*

**7/17/26 - I modified a design for usability**

So I really liked my design for the base pieces, using a dovetail shape for simple moving and replacing. But there was one slight issue, the base_body could literally just slide off the side of the dovetail when the arm was moving. And I knew this was a point of concern, but I hadn't really decided how to fix it until now. Really it was quite simple, I just cut out small slots on both ends of the base_bottom dovetail, and extended the sides a little past the size of the base_body. Then I made a couple little pins that could slide in those slots, and keep the whole thing stuck tightly together, while maintaining the simple switch out I wanted.




*Time Spent: 45 Minutes*

**7/21/26 - I tested and fixed the code**

So now that my replacement power source came in(the first one was missing from the order) I could finally test out the whole setup before assembly! So i got it all wired, double checked my wires, and flashed the code. The arduino instantly displayed it's IP address, so i plugged that into the python code to run the whole system. The python code initaited beautifully, and the GUI looked great. But of course, no system ever works the first time, or usually the second either. And alas, when I moved the arm position in the GUI, i got absolutely no reaction from the servos. My first thought was that the power source wasn't working, so I redid the wiring on that multiple times, still nothing. I did some more research on possible issues, and it seemed like the only viable answer was that either the power connection was bad, or the PCA module was DOA(dead on arrival). But in a moment of clarity, I decided to write a test script that simply moved all the servos with no initation. And that worked perfectly, they all spun and did exactly what they were supposed to. So then I knew it was an issue with the python code, I spent over an hour debugging and redoing things, but for the most part everything seemed good, but the tests still failed. Finally, after hours of testing, I saw my ridicously obvious mistake, I had forgotten to click the 'connect' button in my GUI. Literally a simple click had wasted hours of my time and a significant amount of AI token usage. So I reran the program, clicked the connect button, and it still didn't work. This time I was able to find the issue much sooner, again a stupidly simple fix of the power converter plug falling out of the outlet. After plugging back in and reinitializing, it ran perfectly! All the servos turned as intended and the GUI functioned correctly! After that I spent a little bit of time just editing the code to make the servos spin more smoothly, and a couple other simple updates, but it all worked as intended!



*Time Spent: 2.5 Hours*

**7/22/26 - I started assembly!**

This was my first day of true assembly! Finally after months of work getting to actually put the parts together and set it all up! So I started off with making sure all the servo horns fit in the slots, but of course, they did not. Even with scaling and tolerances and everything they did not fit. So i went through the tedious process, of using a soldering iron to melt out layers of plastic on the inside of the parts. Even after doing this for a while on one part, it still did not fit whatsoever. Then I finally had a 'duh' moment, and realized I could just melt down the servo horn itself to fit better. So in another 15 minutes I had one servo horn that fit perfectly, and got started on the next, which went so much faster with this new technique. Before too long I had them all fitting perfectly and nicely glued in place. I also got the PCA module with it's power plug and the arduino with it's battery all glued into the base.
new2
new

*Time Spent: 2 Hours*

**7/23/26 - I ran the wires and screwed everything in**

Now that I knew most of the parts would fit, the next step was to legnthen the servo wires and run them through each piece. This was a fairly simple and task, I just had to measure and estimate the length I would need for each servo to go from it's piece down to the base, and still have enough extra length so movement isn't restricted. Thankfully since the pack of jumper wires I ordered came with 40 of each male-male, male-female, and female-female wires, I could pretty easily connect each of the servo wires to the PCA module. I also took the time to after connecting each of the three wires, to go every 4 inches or so along them and tape them together in a nice line. This will make sure everything fits nice, looks nice, and no wires get mixed up. Then I just simply slotted each of the servos into place, and screwed them nicely in. For the last one(in the base) I did need to slighty rework it so it would align correctly and the top would close, but that wasn't too hard and didn't require reprinting. And as a last second thought, I decided to add a switch to the arduino battery, becuase otherwise it would always be left on and I didn't want to have to take it apart every night.

old



*Time Spent: 1.5 Hours*

**7/25/26-8/2/26 - I did the final steps!...and they failed**

So the last thing I had to do was screw it all together! And the process itself went quite well, everything attacked as desired, and nothing seemed largely faulty. But when I got it all assembled and started trying to use the GUI to rotate it, there were some obvious issues. Apparently when I had screwed on the pieces to the servos, I had forgotten to make sure the servo position was set to the corresponding angle I was screwing the arm piece on in, so the servo thought it was at 90 degrees but the arm was actually in the 160 degree positions. But that was a simple fix, and before too long I had it all set up correctly this time. And yet again there were issues, the code wasn't communicating correctly with the servos, meaning they moved very slowly at first, then flew towards the position, which would cause any arm to fall over, no matter the stability. So I refactored, and refactored, and refactored, again and again and again, just trying to get it to work how I envisioned. Finally after 5+ hours of work trying to fix it across multiple days, I decided to consult AI coding tools. And before too much longer there was steady progress, the arm would move more smoothly, and the angles were correct. Ultimately it just came down to the fact that the code is a bit beyond what I have truly learned, and I have no problem seeking help when I need it, and since no one in my family can code, obviously the AI came in handy to fix some issues.



*Time Spent: 5.5 Hours(across a couple days of doing the same things over an over)*

**8/5/26 - I printed two pieces**
So I realized that part of the reason the shoulder joint was having so much trouble was because the arm top piece was a bit too heavy, so I decided to reprint it at a much lower infill, since it really wasn't that structural of a piece and could have less strength. It was a simple and fast print, came out well, and I got it all switched out with the old one. It really helped, and gave the shoulder much more strength in general. Also I realized the clips for my base pieces wer starting to break due to being under too much stress, so I actually just snapped all of them off and designed a new piece to glue on that would fix that issue and actually give it a cleaner look. It didn't quite fit right the first time, but it was enough for some testing and the fixes were super simple, so I just threw together the fixed one and it went great.



*Time Spent: 1.5 Hours*

**8/8/26 - I continued to fix issues**
There were a couple slight issues with the yaw still, it seemed that it would not rotate fully due to too much resistance with the clip ring. So i simply scaled it up to 102%, and reprinted, and it worked perfectly. Which goes to show how sometimes your designs can be perfect, but you just need a little more tolerance. After that I also reprinted the gears slightly with just a little longer teeth, which really solved a couple tension issues, and helped me get much better movement. I also realized the screws on the top servo really were not holding it in place, so I went through the simple process of gluing it instead, which should keep it much more secure while keeping the same cleanliness of the previous version. And while I was at it I also replaced the glue in the main body. It had had issues with some parts coming free and wiggling around, so I methodically moving things around and resecured them.



*Time Spent: 2 Hours*

8/10/26 - I fixed the servo jittering 
So even though the mechanical fixes from the other day helped a lot with the weight, the actual movement of the arm still felt way too jerky and unnatural when I tried to use the GUI to rotate it, it would just jump instantly to the target angle instead of gliding there which put a ton of unnecessary momentum and stress on my 3D-printed joints and honestly I was worried it was going to snap something if I kept testing it like that. I knew I needed to dive back into the code to implement proper acceleration pacing, so I sat down for a solid 3 hours to figure out a smoother interpolation system and started breaking down the logic of how the GUI communicates with the micro-controller because instead of just sending a raw destination angle straight to the servo write function, I needed the code to step through the angles gradually. I set up a loop that calculates the distance between the current angle and the target angle and moves the servo in small increments, like 1 or 2 degrees at a time, with a tiny millisecond delay between each step, but at first this made the arm move incredibly slow, almost like it was lagging or breaking, so I spent about an hour tweaking those increment steps and delay intervals trying to find the perfect sweet spot where it moved fluidly without feeling painfully sluggish. Once I got the basic stepping down I noticed a new issue where the arm would start and stop so abruptly that the inertial jerk was still making the main body wiggle, which is the exact issue I've been trying to get away from, so I decided to try implementing a basic easing or acceleration curve. I used the AI coding tools again to help me write a function that would make the servo start moving slowly, speed up in the middle of the arc, and then decelerate right before reaching the final angle, but this took a lot of back-and-forth debugging because the math for the interpolation kept throwing out-of-bounds angles that caused the servos to twitch wildly or hit their physical limits and make terrible buzzing noises. After a ton of refactoring and testing individual axes one by one and constantly uploading the code to see what changed, the code finally stabilized and watching the shoulder and yaw joints glide smoothly to their positions without slamming to a halt was incredibly satisfying and felt like a massive win. 



*Time Spent: 3 Hours*

**8/11/26 - I worked on the fingers and gears**
So today I noticed that the fingers were having a lot of trouble moving because there was just way too much friction between the gears, they kept binding up and clicking instead of moving together smoothly which was super annoying. At first I thought I could just fix it fast without reprinting everything, so I tried trimming them down to give them some more space to turn, but that didn't really work out because it was super tedious and I ended up ruining the shape on one of them which just made it slip completely. Since trimming them by hand was a bust, I went back into my design and decided to reprint all of the gears instead, but this time I made the whole gears thicker so they would fit much better in their slots, and I also made the teeth shorter on a few of them so they wouldn't jam into each other anymore. It took about two hours to get all the new parts printed and swapped out, and since they just seat right into place without needing screws it was pretty fast to test, and once I got them all put into the hand assembly it worked a lot better and the fingers actually close now without grinding or locking up on me. 




*Time Spent: 2 Hours*

**8/13/26 - I added the final touches and tested**
The last couple things to do were to one: add spacers in between the arm joints so they didn't wobble so much. And two: add grips to the end of the fingers for, well, grip. Both went off without a hitch, since I literally just modeled the spacers off the end of their respective parts, it was super easy to do and to make fit. After that I just cut up an extra strip of TPU I had lying around and glued it onto the ends of the fingers for a nice grip. Then I decided to finally fix the one issue that had been bugging me from the start: not enough power. So I ordered a power supply with slightly higher volts and amps, and it really helped, giving each joint that much more power meant no slow rising or random brownouts. And to finish it all off, I tested it by playing back a prerecorded movement sequence, and it all worked together beautifully.




*Time Spent: 1 Hour*

**8/14/26 - I finished my project**
Well it works. After all the long days and late nights and way too much redesigning and reimplementing, I have a functioning robotic arm. And this might not seem like a big deal to some people, but to me this means the world. Because it was never just about having a robotic arm, it was to learn the process, the fundamentals, the ideas, and how that all fits together to make something work. And honestly I'd say I achieved that, even if it took a lot of wasted parts and stressful days, I gained so much valuable experience that really makes the whole thing pay off. This really excites me for all the opportunities down the road to do the same thing, learn through trial and error. Which really is not fun at first, but the payout is astounding. And to think I didn't know any of this 5 months ago when I started, really puts it in perspective of how much I have learned and grown in. A huge thanks to Hack Club for the funding that made this happen, and for all their help along the way. ARC-3 is now officially completed.



*Time Spent: 15 minutes writing this and an hour reveling in it*

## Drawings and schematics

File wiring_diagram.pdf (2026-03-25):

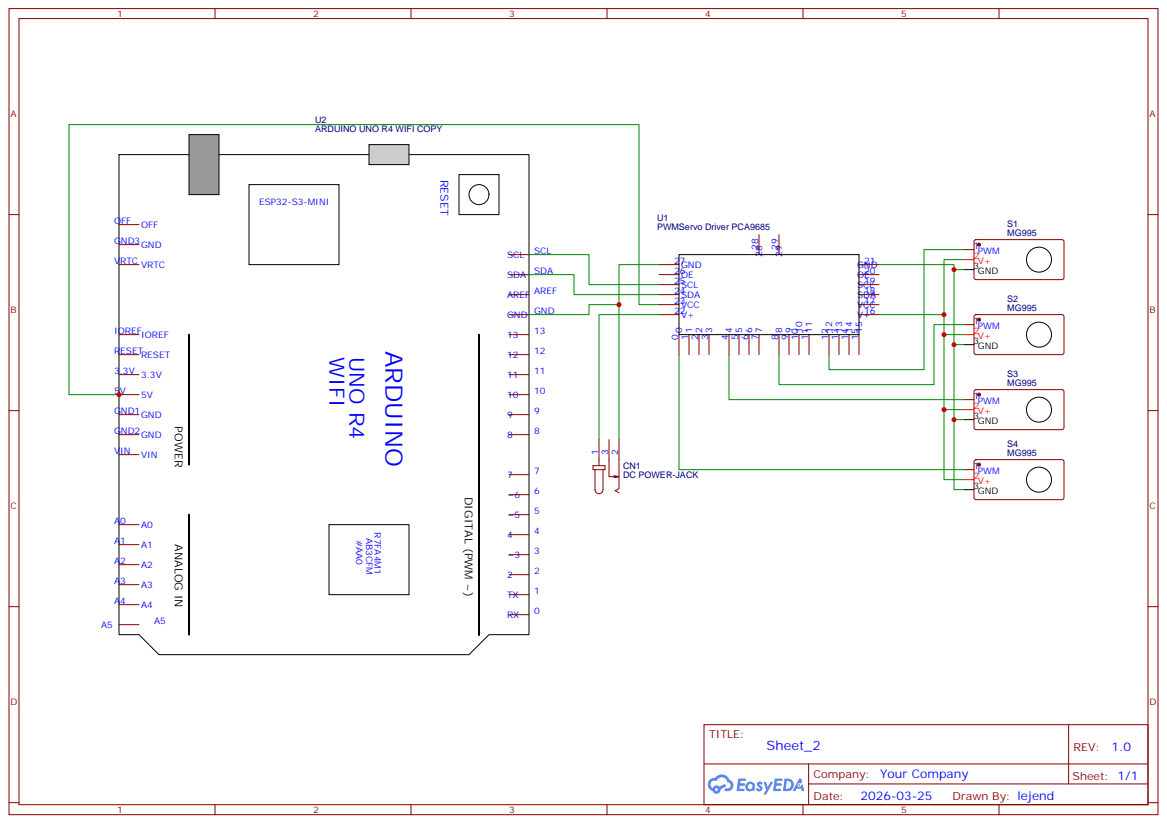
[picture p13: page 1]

ARDUINO UNO R4 WIFI COPY

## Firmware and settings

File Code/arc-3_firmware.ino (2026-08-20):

#include <Wire.h> 
#include <Adafruit_PWMServoDriver.h> 
#include <WiFiS3.h> 


const char* WIFI_SSID     = "YourWIFIName"; 
const char* WIFI_PASSWORD = "YourWIFIPassword"; 
const int   SERVER_PORT   = 8888; 


#define USE_STATIC_IP 1
#if USE_STATIC_IP
IPAddress LOCAL_IP(YourAvailableDesiredIP);
IPAddress GATEWAY_IP(YourRoutersIP);
IPAddress SUBNET_MASK(YourSubnetMask);
#endif


Adafruit_PWMServoDriver pca = Adafruit_PWMServoDriver(0x40); 

#define CH_YAW      0 
#define CH_SHOULDER 1 
#define CH_ELBOW    2 
#define CH_CLAW     3 

#define PULSE_MIN_US 500 
#define PULSE_MAX_US 2400 

const float ANGLE_MIN[4] = { 0.0f,   0.0f,   0.0f,   0.0f   }; 
const float ANGLE_MAX[4] = { 180.0f, 260.0f, 180.0f, 180.0f }; 
const float HOME_POS[4]  = { 90.0f,  70.0f,  90.0f,  0.0f   }; 
float targetAngles[4]    = { 90.0f,  70.0f,  90.0f,  0.0f   }; 
float servoAngles[4]     = { 90.0f,  70.0f,  90.0f,  0.0f   }; 
uint16_t lastWrittenPulse[4] = {0, 0, 0, 0};


#define SLEW_TICK_MS 20
#define SLEW_EPS 0.5f
const float SLEW_STEP_DEG[4] = { 3.0f, 3.0f, 3.0f, 1.5f };  
#define REASSERT_MS 500        
#define TEST_STEP_DEG 2.0f    

WiFiServer server(SERVER_PORT); 
WiFiClient client; 
String cmdBuffer = ""; 
String serialCmdBuffer = "";
unsigned long lastActivityMs = 0; 
unsigned long lastWifiPollMs = 0;
unsigned long lastWifiRetryMs = 0;
bool wifiReady = false;
#define CLIENT_TIMEOUT_MS 8000 
#define WIFI_RETRY_MS 10000   


bool testActive = false;
int  testChannel = -1;
float testPos = 0.0f;
int  testPhase = 0;


void homeServos();
void setTargets(const float vals[]);
void writeServoPulse(uint8_t channel, float angle);
void updateMotion();
void reassertServos();
void processSerialInput();
void handleCommand(const String& cmd, Print& out, bool replyToSetAll);

void setup() { 
  Serial.begin(115200); 
  delay(500); 

  Wire.begin(); 
  Wire.setWireTimeout(50000, true);  
  if (!pca.begin()) {
    Serial.println("[ERROR] PCA9685 servo driver NOT found on I2C (address 0x40).");
    Serial.println("        Check SDA/SCL wiring, VCC, and that address jumpers = 0x40.");
  } else {
    pca.setPWMFreq(50); 
    Serial.println("[OK] PCA9685 servo driver detected.");
  }
  delay(100); 

  
  homeServos(); 
  Serial.println("Servos initialized at home position."); 

 
  Serial.print("Connecting to WiFi network: "); 
  Serial.println(WIFI_SSID); 
#if USE_STATIC_IP
  WiFi.config(LOCAL_IP, GATEWAY_IP, SUBNET_MASK);
  Serial.println("Using static IP address.");
#endif
  WiFi.begin(WIFI_SSID, WIFI_PASSWORD); 

  int tries = 0; 
  while (WiFi.status() != WL_CONNECTED) { 
    processSerialInput();
    delay(500); 
    Serial.print("."); 
    if (++tries > 16) { 
      Serial.println("\n[WARN] WiFi failed. Continuing in USB serial mode."); 
      break;
    } 
  } 

  if (WiFi.status() == WL_CONNECTED) {
    wifiReady = true;
    delay(1000); 

    Serial.println("\n==========================================");
    Serial.print("Connected successfully! IP Address: "); 
    Serial.println(WiFi.localIP()); 
    Serial.print("Signal Strength (RSSI): "); 
    Serial.print(WiFi.RSSI());
    Serial.println(" dBm"); 
    Serial.println("==========================================");

    server.begin(); 
    Serial.println("Server listening on port 8888..."); 
  }
  Serial.println("USB serial command mode ready at 115200 baud.");
} 

void loop() { 
  processSerialInput();

  
  updateMotion();
  reassertServos();

  
  if (!wifiReady) {
    if (WiFi.status() == WL_CONNECTED) {
      wifiReady = true;
      server.begin();
      Serial.println("\n[OK] WiFi (re)connected. IP: " + String(WiFi.localIP()));
    } else if (millis() - lastWifiRetryMs >= WIFI_RETRY_MS) {
      lastWifiRetryMs = millis();
      Serial.println("[WIFI] Connecting to " + String(WIFI_SSID) + "...");
      WiFi.begin(WIFI_SSID, WIFI_PASSWORD);
    }
    return;
  }

  
  if (WiFi.status() != WL_CONNECTED) {
    wifiReady = false;
    if (client) {
      client.stop();
      client = WiFiClient();
    }
    Serial.println("[WIFI] Link lost - auto-reconnect enabled.");
    return;
  }

  
  if (millis() - lastWifiPollMs < 2) {
    return;
  }
  lastWifiPollMs = millis();

  
  if (!client || !client.connected()) { 
    if (client) { 
      client.stop(); 
      Serial.println("Client disconnected."); 
    } 
    WiFiClient incoming = server.available(); 
    if (incoming) { 
      client = incoming; 
      cmdBuffer = ""; 
      lastActivityMs = millis(); 
      Serial.print("Client connected from IP: "); 
      Serial.println(client.remoteIP()); 
    } 
  } 

  
  if (client && client.connected()) { 
    if (millis() - lastActivityMs > CLIENT_TIMEOUT_MS) { 
      Serial.println("Client inactive. Connection timed out."); 
      client.stop(); 
      return; 
    } 
    while (client.available()) { 
      char c = client.read(); 
      lastActivityMs = millis(); 
      if (c == '\n') { 
        cmdBuffer.trim(); 
        if (cmdBuffer.length() > 0) {
          handleCommand(cmdBuffer, client, false); 
        }
        cmdBuffer = ""; 
      } else if (c != '\r') { 
        cmdBuffer += c; 
        if (cmdBuffer.length() > 256) cmdBuffer = ""; 
      } 
    } 
  } 
} 

void processSerialInput() {
  while (Serial.available()) {
    char c = Serial.read();
    if (c == '\n') {
      serialCmdBuffer.trim();
      if (serialCmdBuffer.length() > 0) {
        handleCommand(serialCmdBuffer, Serial, false);
      }
      serialCmdBuffer = "";
    } else if (c != '\r') {
      serialCmdBuffer += c;
      if (serialCmdBuffer.length() > 256) serialCmdBuffer = "";
    }
  }
}

void handleCommand(const String& cmd, Print& out, bool replyToSetAll) { 
  if (cmd == "PING") { 
    out.println("PONG"); 
  }  
  else if (cmd == "STATUS") { 
    if (wifiReady) {
      out.print("IP:"); 
      out.println(WiFi.localIP()); 
    } else {
      out.println("USB:READY");
    }
  }  
  else if (cmd == "GET") { 
    out.print(targetAngles[0]); out.print(","); 
    out.print(targetAngles[1]); out.print(","); 
    out.print(targetAngles[2]); out.print(","); 
    out.println(targetAngles[3]); 
  }  
  else if (cmd.startsWith("TEST:")) { 
    int ch = cmd.substring(5).toInt(); 
    if (ch >= 0 && ch < 4) { 
      testActive = true; 
      testChannel = ch; 
      testPos = servoAngles[ch]; 
      testPhase = 0; 
      out.println("OK TESTING:" + String(ch)); 
    } else { 
      out.println("ERR:CHANNEL"); 
    } 
  }  
  else if (cmd == "STOP") {
    testActive = false;
    testChannel = -1;
    out.println("OK");
  }
  else if (cmd.startsWith("SETALL:")) { 
    String data = cmd.substring(7); 
    float vals[4]; 
    int found = 0; 
    int startIdx = 0; 

   
    for (int i = 0; i < data.length(); i++) { 
      if (data.charAt(i) == ',' || i == data.length() - 1) { 
        int endIdx = (i == data.length() - 1) ? i + 1 : i; 
        vals[found] = data.substring(startIdx, endIdx).toFloat(); 
        found++; 
        startIdx = i + 1; 
        if (found >= 4) break; 
      } 
    } 

    if (found == 4) { 
      setTargets(vals); 
      if (replyToSetAll) out.println("OK");
    } else { 
      out.println("ERR:BAD_FORMAT"); 
    } 
  }  
  else { 
    out.println("ERR:UNKNOWN"); 
  } 
} 

void writeServoPulse(uint8_t channel, float angle) { 
  float t = constrain((angle - ANGLE_MIN[channel]) / (ANGLE_MAX[channel] - ANGLE_MIN[channel]), 0.0f, 1.0f); 
  float pulseUs = PULSE_MIN_US + t * (PULSE_MAX_US - PULSE_MIN_US); 
  uint16_t targetPulse = (uint16_t)constrain(pulseUs, 400, 2600); 
  if (abs((int)targetPulse - (int)lastWrittenPulse[channel]) >= 2) {
    pca.writeMicroseconds(channel, targetPulse); 
    lastWrittenPulse[channel] = targetPulse;
  }
}

void homeServos() { 
  for (int i = 0; i < 4; i++) { 
    targetAngles[i] = HOME_POS[i]; 
    servoAngles[i]  = HOME_POS[i]; 
    writeServoPulse(i, HOME_POS[i]); 
  } 
}

void setTargets(const float vals[]) { 
  for (int i = 0; i < 4; i++) { 
    targetAngles[i] = constrain(vals[i], ANGLE_MIN[i], ANGLE_MAX[i]); 
  } 
}

void updateMotion() { 
  static unsigned long lastSlewMs = 0; 
  static int slewCursor = 0; 
  unsigned long now = millis(); 

  
  if (testActive && testChannel >= 0 && testChannel < 4) { 
    if (now - lastSlewMs >= SLEW_TICK_MS) { 
      lastSlewMs = now; 
      if (testPhase == 0) { 
        testPos += TEST_STEP_DEG; 
        if (testPos >= ANGLE_MAX[testChannel]) { testPos = ANGLE_MAX[testChannel]; testPhase = 1; } 
      } else { 
        testPos -= TEST_STEP_DEG; 
        if (testPos <= ANGLE_MIN[testChannel]) { testPos = ANGLE_MIN[testChannel]; testPhase = 0; } 
      } 
      servoAngles[testChannel] = testPos; 
      writeServoPulse(testChannel, testPos); 
    } 
    return; 
  } 

  if (now - lastSlewMs < SLEW_TICK_MS) return; 
  lastSlewMs = now; 

  
  for (int i = 0; i < 4; i++) { 
    int ch = (slewCursor + i) % 4; 
    float diff = targetAngles[ch] - servoAngles[ch]; 
    if (fabsf(diff) > SLEW_EPS) { 
      float step = SLEW_STEP_DEG[ch]; 
      servoAngles[ch] += (diff > 0 ? step : -step); 
      if (fabsf(targetAngles[ch] - servoAngles[ch]) < step) servoAngles[ch] = targetAngles[ch]; 
      writeServoPulse(ch, servoAngles[ch]); 
      slewCursor = (ch + 1) % 4; 
      return; 
    } 
  } 
  slewCursor = (slewCursor + 1) % 4; 
} 

void reassertServos() { 
  static unsigned long lastReassertMs = 0; 
  unsigned long now = millis(); 
  if (now - lastReassertMs < REASSERT_MS) return; 
  lastReassertMs = now; 
  for (int i = 0; i < 4; i++) { 
    float t = constrain((servoAngles[i] - ANGLE_MIN[i]) / (ANGLE_MAX[i] - ANGLE_MIN[i]), 0.0f, 1.0f); 
    uint16_t p = (uint16_t)constrain(PULSE_MIN_US + t * (PULSE_MAX_US - PULSE_MIN_US), 400, 2600); 
    pca.writeMicroseconds(i, p); 
    lastWrittenPulse[i] = p; 
  } 
}

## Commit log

2026-03-21 CAD file 1
2026-03-21 Update CAD
2026-03-21 CAD files
2026-03-21 Add CAD files of ARC-3 arm
2026-03-21 Create BOM.csv with item specifications
    Added a Bill of Materials (BOM) with item details, quantities, and links.
    [BOM.csv]
2026-03-21 Enhance README with detailed project specifications
    Expanded project description to include specific components and power requirements.
2026-03-23 Update README with arm segment design details
2026-03-23 Fix formatting and currency in BOM.csv
    [BOM.csv]
2026-03-23 Update README with arm design and wiring details
2026-03-24 Update BOM.csv with new components and corrections
    [BOM.csv]
2026-03-24 Update README with finger design and alignment details
2026-03-25 edited BOM
    [BOM.csv]
2026-03-25 fixed files
    [arm_top.f3z, arm_top.step, base_body.f3d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]
2026-03-25 added CAD files
    [Fingers.f3d, Fingers.step, gears.f3z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]
2026-03-25 Update README with design details for fingers and base
2026-03-25 added wiring diagram
2026-03-26 edited files
    [arm_bottom.f3z, arm_bottom.step, assembly_with_electronics.step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]
